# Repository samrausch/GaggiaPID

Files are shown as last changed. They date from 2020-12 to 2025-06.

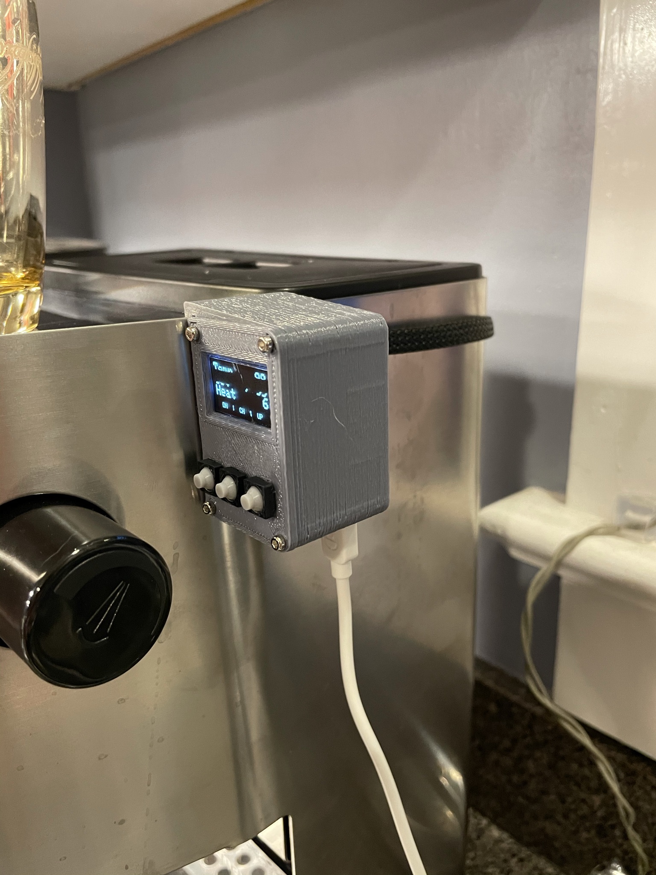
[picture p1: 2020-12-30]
Photos/IMG_0123.JPEG

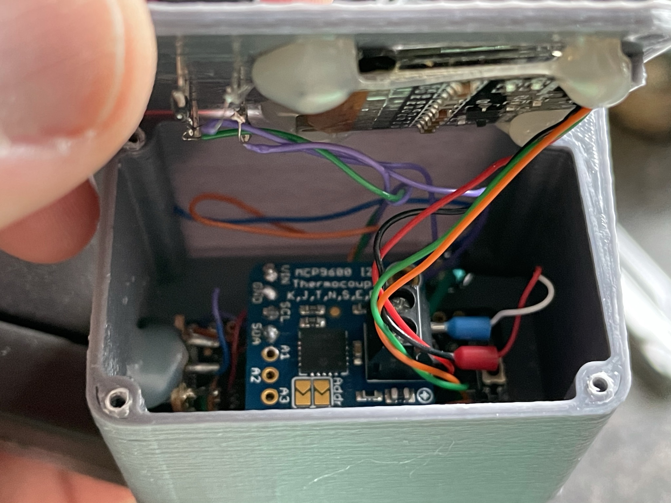
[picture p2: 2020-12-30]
Photos/IMG_0134.JPEG

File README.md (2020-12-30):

# GaggiaPID
Open Source PID for Gaggia Classic and Classic Pro espresso machines

As seen on https://www.reddit.com/r/gaggiaclassic/comments/kmm09a/diy_pid_for_my_gaggia_classic/

The .ino file includes several libraries.  Please make sure you've downloaded them prior to uploading the code to your Arduino of choice.  This was built on an Adafruit Metro Mini, which is directly compatible with the Arduino Uno R3, but you can use any Arduino board as long as it has enough pins and it supports I2C.

The code is reasonably well commented internally and variables are named such that it should be easy to find values you may need to change for your specific implementation, such as which pins have buttons assigned to them or the output pin for the SSR.

This design is intended to be as simple as possible in terms of the installation, and requires minimal modification to the Gaggia machine.  You'll need the following parts, as well as basic soldering tools/skills and access to a 3D printer (if you choose to use the included .stl files)

* Arduino board of your choice
* MCP9600 thermocouple amp (https://www.adafruit.com/product/4101)
* M4 threaded K-type thermocouple (widely available from Amazon, etc as a replacement part for 3D printers)
* 128x64 I2C OLED screen (substitute any screen you prefer but you'll need to update the code for your specific unit)
* 3 buttons (I used these: https://www.aliexpress.com/item/32811149954.html?spm=a2g0s.9042311.0.0.49554c4dRzoluB)
* M2x8mm screws of your choise (I used these: https://www.amazon.com/gp/product/B00YBMRAH4/ref=ppx_yo_dt_b_search_asin_title?ie=UTF8&psc=1)
* Solid state relay (I used this: https://www.amazon.com/gp/product/B07Y33RZ8F/ref=ppx_yo_dt_b_search_asin_title?ie=UTF8&psc=1)
* Rare earth magnets (optional), attached to the back of the SSR to fasten it to the inside of the espresso machine.
* Braided cable sleeve (optional), I used https://www.amazon.com/gp/product/B07QJW9FKS/ref=ppx_yo_dt_b_search_asin_title?ie=UTF8&psc=1

# 3D printing

I printed everything using Inland PLA+ filament.  Pretty much any material should work fine as the outside of the Gaggia never gets hot enough to melt most thermoplastics.  The included STL files assume you're using the exact same parts I am.  If you use anything different you'll need to make adjustments to the 3D printed parts.

There are no holes in the printed parts for the wiring between the PID and espresso machine, you'll need to decide where you want these holes and drill them yourself.

In it's current revision, the Arduino board is still powered via USB so there needs to be an opening to plug in the USB cable.  This opening is also not included in the STL files as it's easier to locate the hole during the assembly.

# Assembly

Follow the included circuit diagram.  For the wiring inside the PID I just used 32AWG single strand hookup wire and for any wiring inside the Gaggia I used silicone insulated wire (26AWG for the wiring from PID to SSR, 12AWG to extend the thermoswitch leads to the SSR as referenced in the Installation Steps below).  The boiler in the Gaggia can get hot enough to melt non-silicone insulation so if you don't have silicone wiring, make sure to keep any wiring well clear of the boiler.

The Arduino board is secured using a small amount of hot glue.  The MCP9600 board is fastened with a screw to the small ledge inside the 3D printed box.  The OLED and buttons can be secured with your favorite adhesive.  The lid of the enclosure is held by four screws.  I drilled pilot holes for all the screws because my 3D printer has problems printing holes that small.  You will probably want to drill pilot holes as well to prevent cracking the plastic.

My PID is just held on by the clip on the side of the 3D printed box.  Gravity seems to be working as expected in my case but you may decide to attach a magnet to the side of the box that touches the Gaggia for a more secure mount.  If you do this, consider counter-sinking the magnet so that it is flush with the outisde of the box.  This will keep things looking tidy.

# Installation steps:

* THIS ASSUMES YOUR COMPETENT WORKING WITH AC CIRCUITS.  AC CIRCUITS ARE DANGEROUS AND MISTAKES CAN CAUSE INJURY OR DEATH.  YOU ALONE ARE RESPONSIBLE FOR YOUR OWN SAFETY, PLEASE KNOW YOUR LIMITS.
* Remove the top of the machine and locate the boiler thermal switch.  This will be the one at the bottom of the boiler, closest to the group head.
* Remove this thermal switch and replace it with the M4 thermocouple, making sure to add thermal compound if necessary.  The thermocouple should be snug but not too tight as the threads are not super robust.
* Run the TC leads out through the back of the machine and into the PID, attaching to the MCP9600.
* Connect the two leads you removed from the original thermal switch to the switched AC side of the SSR.  You may need to extend the leads depending on where you decide to mount the SSR.  They are not polarized so you can connect either one to either terminal of the SSR.
* Connect the +/- leads from the PID to the SSR input terminals, paying attention to the polarity as these are DC.
* Mount the SSR as desired.
* Optionally, you can add some sleeving to the wires running between the Gaggia and the PID.  If you do this, secure a zip tie to the end of the sleeve inside the machine to keep it from pulling out.
* Test that everything is working before closing the machine back up.

There's a circuit diagram included in the repo.  You're welcome to wire your PID however you like but make sure to change any pin numbers in the code to reflect how you've assembeled the circuit.

The PID has been setup with values for Kp, Ki and Kd that work adequately but you may want to adjust them to suit your needs.  The PID values are not saved if you change them through the menu so if you find a tuning you like and want to change the defaults, you'll need to do that in the code and then re-upload it to the device.

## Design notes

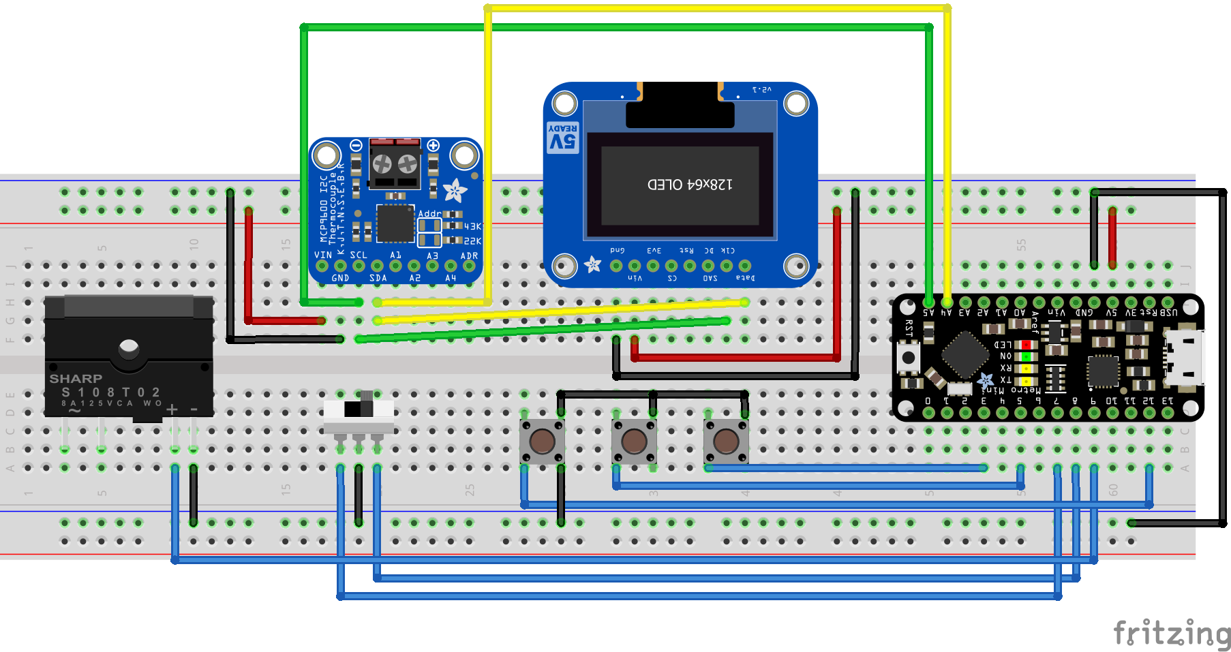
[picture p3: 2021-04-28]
GaggiaPID_circuit.png

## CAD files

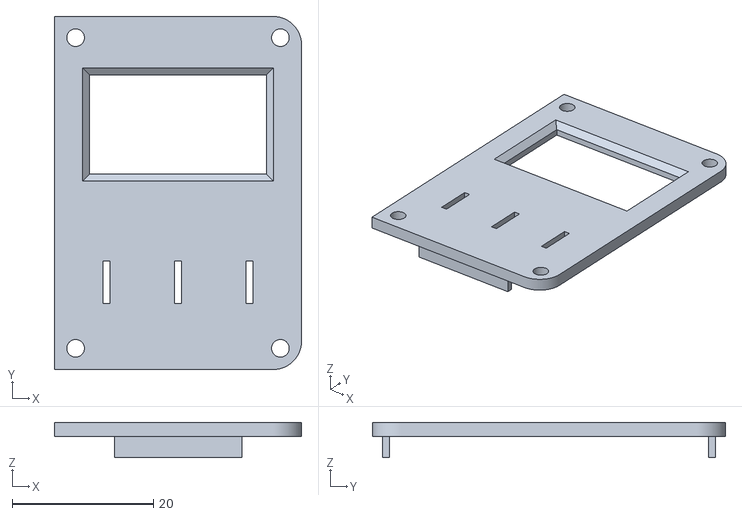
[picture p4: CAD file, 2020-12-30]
GaggiaPID_top.stl
35.0 x 50.0 x 5.00

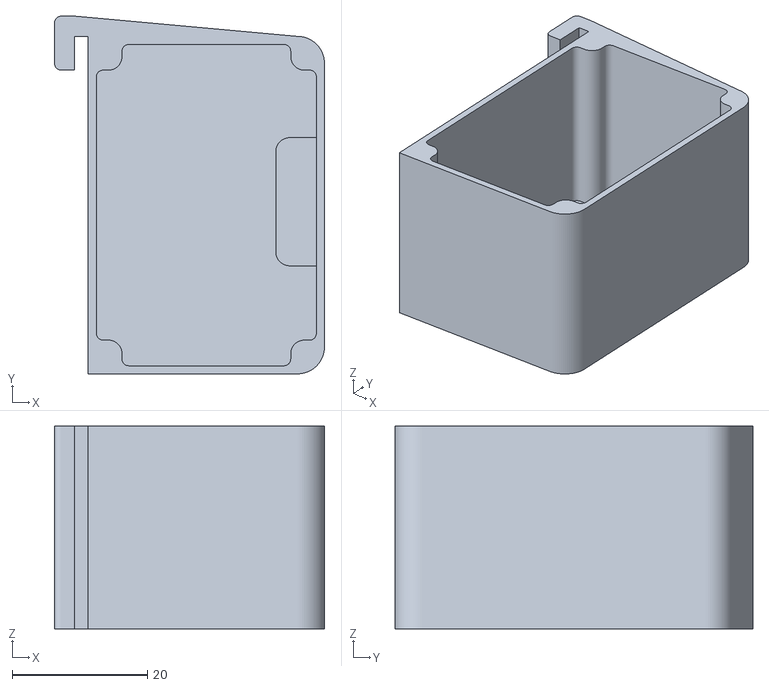
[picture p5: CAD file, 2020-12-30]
GaggiaPID_body.stl
40.0 x 53.0 x 30.0

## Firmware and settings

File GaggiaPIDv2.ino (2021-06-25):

#include <Adafruit_MCP9600.h>
#define tc_address (0x67)
Adafruit_MCP9600 mcp;

#include <Bounce2.h>
Bounce modeButton = Bounce();
Bounce upButton = Bounce();
Bounce downButton = Bounce();
const unsigned long intervalMs = 5;

#define NOOP __asm__ __volatile__ ("nop\n\t")

// if you're using a 128x64 i2c OLED, this is all you need
// if you're using something else, feel free to substitute your stuff here
#include <Adafruit_SSD1306.h>
#include <gfxfont.h>
#include <Adafruit_GFX.h>
#define SCREEN_WIDTH 128 // OLED display width, in pixels
#define SCREEN_HEIGHT 64 // OLED display height, in pixels
#define OLED_RESET 4
Adafruit_SSD1306 display(SCREEN_WIDTH, SCREEN_HEIGHT, &Wire, OLED_RESET);

#include <Wire.h> 
// This stuff is just for text formatting so you can control the indents and line spacing
// if you're using a 128x64 OLED screen, you can keep all these values
// otherwise you'll want to change them depending on your display
const int indent1 = 88;
const int indent2 = 72;
const int bottom = 56;
const int line1 = 0;
const int line2 = 16;
const int line3 = 32;
const int upPin = 3;
const int modePin = 12;
const int downPin = 5;
const int relayPin = 9;
const int runPin = 7;
const int progPin = 8;
int brewTemp = 93;      // set the default brew temp here
int steamTemp = 155;    // set the default steam temp here
int runMode = 1;
int brewMode = 1;
int firstRun = 1;

#include <PID_v1.h>
double targetTemp;
double currentTemp;
double heatState;
double Kp = 10;
double Ki = 50;
double Kd = 30;
PID myPID(&currentTemp, &heatState, &targetTemp, Kp, Ki, Kd, DIRECT);
int WindowSize = 100;
unsigned long windowStartTime;

void setup() {
  pinMode(relayPin, OUTPUT);
  pinMode(runPin, INPUT_PULLUP);
  pinMode(progPin, INPUT_PULLUP);
  display.begin(SSD1306_SWITCHCAPVCC, 0x3C);
  display.clearDisplay();
  display.setCursor(0,0);
  display.setTextSize(2);
  display.setTextColor(WHITE);
  display.println("Gaggia PID");
  display.println("v2.0");
  display.println("Now with STEAM!");
  if (! mcp.begin(tc_address)) {
    display.clearDisplay();
    display.println("TC ERROR");
    display.display();
    while (1);
  }
  mcp.setADCresolution(MCP9600_ADCRESOLUTION_18);
  mcp.setThermocoupleType(MCP9600_TYPE_K);
  mcp.setFilterCoefficient(3);
  mcp.enable(true);
  
  display.display();
  
  delay(1000);
  display.clearDisplay();
  display.setCursor(0,0);
  display.setTextSize(2);
  display.println("Temp");
  display.println("Set -->");
  display.println("Heat");
  display.setCursor(0,bottom);
  display.setTextSize(1);
  display.print("  DN  |  ST  |  UP  ");
  display.display();
  pinMode(modePin, INPUT_PULLUP);
  pinMode(upPin, INPUT_PULLUP);
  pinMode(downPin, INPUT_PULLUP);
  modeButton.attach(modePin);
  modeButton.interval(intervalMs);
  upButton.attach(upPin);
  upButton.interval(intervalMs);
  downButton.attach(downPin);
  downButton.interval(intervalMs);
  windowStartTime = millis();
  targetTemp = brewTemp;
  myPID.SetOutputLimits(0, WindowSize);
  myPID.SetMode(AUTOMATIC);
}

void brewDisplay() {
  // this function updates the display when in brew/steam mode
  display.clearDisplay();
  display.setCursor(0,0);
  display.setTextSize(2);
  display.println("Temp");
  if (brewMode == 1) {
    display.println("Brew  >");
  }
  if (brewMode == 2) {
    display.println("Steam >");
  }
  display.println("Heat");
  display.setCursor(indent1,line1);
  if (currentTemp < 100){
    display.print(" ");
  }
  display.print(int(currentTemp));
  display.setCursor(indent1,line2);
  if (targetTemp < 100){
    display.print(" ");
  }
  display.print(int(targetTemp));
  display.setCursor((indent1-12),line3);
  int heatDuty = map(heatState, 0, WindowSize, 0, 100);
  if (heatDuty < 1000){
    display.print(" ");
  }
  if (heatDuty < 100){
    display.print(" ");
  }
  if (heatDuty < 10){
    display.print(" ");
  }
  display.print(int(heatDuty));
  display.setCursor(0,bottom);
  display.setTextSize(1);
  display.print("  DN  |  ST  |  UP  ");
  display.display();
}

void PIDdisplay() {
  // this function updates the display when it's in programming mode
  display.clearDisplay();
  display.setCursor(0,0);
  display.setTextSize(2);
  display.println("P ");
  display.println("I ");
  display.println("D ");
  display.setCursor(indent2,line1);
  display.print(int(Kp));
  display.setCursor(indent2,line2);
  display.print(int(Ki));
  display.setCursor(indent2,line3);
  display.print(int(Kd));
  display.setCursor(0,bottom);
  display.setTextSize(1);
  display.print("  DN  |  CH  |  UP  ");
  display.setTextSize(2);
  switch (runMode) {
    case 1:
      display.setCursor(0,line1);
      display.print("  -->");
      break;
    case 2:
      display.setCursor(0,line2);
      display.print("  -->");
      break;
    case 3:
      display.setCursor(0,line3);
      display.print("  -->");
  }
  display.display();
}

void checkButtons() {
  // there's a lot going on in here
  // first we check the buttons to see if they've been pressed
  int modeSelect = 1;
  byte modeButtonState = modeButton.read();
  byte upButtonState = upButton.read();
  byte downButtonState = downButton.read();
  int amIrunning = digitalRead(runPin);
  // this is the swtich that goes between run and programming, connected to the runPin
  if (amIrunning == 0) {
    modeSelect = 1; //brewing
    brewDisplay();
  } else {
    modeSelect = 2; //programming
    PIDdisplay();
  }
  switch (modeSelect) {
    case 1: // we're brewing
      modeButton.update();
      modeButtonState = modeButton.read();
      // this section changes between steam and brew based on the brewMode variable, which is toggled by the mode button
      if (modeButtonState == LOW && modeButton.fallingEdge()) {
        switch (brewMode) {
          case 1: // Switch to steam
            brewMode = 2;
            brewTemp = targetTemp;
            targetTemp = steamTemp;
            //brewDisplay();
            break;
          case 2: // Switch to brew
            brewMode = 1;
            steamTemp = targetTemp;
            targetTemp = brewTemp;
            //brewDisplay();
        }
      }
      upButton.update();
      upButtonState = upButton.read();
      // here we're raising the temp of brew or steam
      if (upButtonState == LOW && upButton.fallingEdge()) {
        switch(brewMode) {
          case 1: // Adjust brew temp settings
            targetTemp++;
            //brewDisplay();
            break;
          case 2: // Adjust steam temp settings
            targetTemp++;
            //brewDisplay();    
        }
      }
      downButton.update();
      downButtonState = downButton.read();
      // here we're lowering the temp of brew or steam
      if (downButtonState == LOW && downButton.fallingEdge()) {
        switch(brewMode) {
          case 1: // Adjust brew temp settings
            targetTemp--;
            //brewDisplay();
            break;
          case 2: // Adjust steam temp settings
            targetTemp--;
            //brewDisplay();
        }
      }
      break;
    case 2: // we're programming
      modeButton.update();
      modeButtonState = modeButton.read();
      // since we're in programming mode, the buttons now control the PID variables
      if (modeButtonState == LOW && modeButton.fallingEdge()) {
        switch (runMode) {
          case 1: // Switch to Ki setting
            runMode = 2;
            //PIDdisplay();
            break;
          case 2: // Switch to Kd setting
            runMode = 3;
            //PIDdisplay();
            break;
          case 3: // Switch to Kp setting
            runMode = 1;
            //PIDdisplay();
        }
      }
      upButton.update();
      upButtonState = upButton.read();
      if (upButtonState == LOW && upButton.fallingEdge()) {
        switch(runMode) {
          case 1: // Adjust Kp settings
            Kp++;
            myPID.SetTunings(Kp, Ki, Kd);
            //PIDdisplay();
            break;
          case 2: // Adjust Ki setting
            Ki++;
            myPID.SetTunings(Kp, Ki, Kd);
            //PIDdisplay();
            break;
          case 3: // Adjust Kd setting
            Kd++;
            myPID.SetTunings(Kp, Ki, Kd);
            //PIDdisplay();       
        }
      }
      downButton.update();
      downButtonState = downButton.read();
      if (downButtonState == LOW && downButton.fallingEdge()) {
        switch(runMode) {
          case 1: // Adjust Kp settings
            Kp--;
            myPID.SetTunings(Kp, Ki, Kd);
            //PIDdisplay();
            break;
          case 2: // Adjust Ki setting
            Ki--;
            myPID.SetTunings(Kp, Ki, Kd);
            //PIDdisplay();
            break;
          case 3: // Adjust Kd setting
            Kd--;
            myPID.SetTunings(Kp, Ki, Kd);
            //PIDdisplay();
        }      
      }
  }
}

void loop() {
  checkButtons();   // see in-line documentation in the function above
  if (millis() - windowStartTime > WindowSize)
    // this is where we periodically read the TC, update the PID and then reset the timer for the next cycle
  { 
    currentTemp = mcp.readThermocouple();
    analogWrite(relayPin, map(heatState, 0, 100, 0, 1023));
    myPID.Compute();
    windowStartTime += WindowSize;
    if (firstRun) {
      delay(1000);
      brewDisplay();
      firstRun = 0;
    }
  }
}

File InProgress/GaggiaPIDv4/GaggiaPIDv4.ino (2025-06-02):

//#define debug

#include <WiFi.h>
#include <WiFiClient.h>
#include <WebServer.h>
#include <LEAmDNS.h>

#ifndef STASSID
#define STASSID "wifi_network"
#define STAPSK "wifi_password"
#endif

const char* ssid = STASSID;
const char* password = STAPSK;

WebServer server(80);

#include <Adafruit_MCP9600.h>
#define tc_address (0x67)
Adafruit_MCP9600 tc;

#include <Bounce2.h>
Bounce2::Button modeButton = Bounce2::Button();
Bounce2::Button upButton = Bounce2::Button();
Bounce2::Button downButton = Bounce2::Button();
//Bounce modeButton = Bounce();
//Bounce upButton = Bounce();
//Bounce downButton = Bounce();
int modePushCounter = 0;
int modeDebounced = 0;
int modeLastDebounced = 0;
bool modePressed = false;
const unsigned long intervalMs = 5;

#define NOOP __asm__ __volatile__("nop\n\t")

#include <Adafruit_SSD1306.h>
#include <gfxfont.h>
#include <Adafruit_GFX.h>

#define SCREEN_WIDTH 128
#define SCREEN_HEIGHT 64
#define OLED_RESET 4
Adafruit_SSD1306 display(SCREEN_WIDTH, SCREEN_HEIGHT, &Wire, OLED_RESET);

#include <Wire.h>

const int indent1 = 88;
const int indent2 = 72;
const int bottom = 56;
const int line1 = 0;
const int line2 = 16;
const int line3 = 32;
const int upPin = 27;    // Pi Pico pin
const int modePin = 26;  // Pi Pico pin
const int downPin = 28;  // Pi Pico pin
const int relayPin = 9;  // Pi Pico pin
int operatingMode = 1;   // 1=brew 2=steam
int configureMode = 1;   // 1=operate 2=configure
int PIDparam = 1;        // 1=Kp 2=Ki 3=Kd
int steamTemp = 140;     // default steam temp
int brewTemp = 85;       // default brew temp


#include <PID_v1.h>
double targetTemp;
double currentTemp;
double heatState;
double Kp = 70;
double Ki = 0.1;
double Kd = 1;
PID myPID(&currentTemp, &heatState, &targetTemp, Kp, Ki, Kd, DIRECT);
int WindowSize = 500;
int calcSize = 250;
unsigned long windowStartTime;
unsigned long calcStartTime;


void setup() {
  Serial.begin(9600);
#ifdef debug
  Serial.println("Debugging enabled...");
#endif
  Wire.setSDA(0);
  Wire.setSCL(1);
  Wire.begin();
  pinMode(relayPin, OUTPUT);
  display.begin(SSD1306_SWITCHCAPVCC, 0x3C);
  display.clearDisplay();
  display.setCursor(0, 0);
  display.setTextSize(2);
  display.setTextColor(WHITE);
  display.println("Gaggia PID");
  display.println("Pico");
  display.println("v1.0");
  delay(2000);
  if (!tc.begin(tc_address)) {
    display.clearDisplay();
    display.println("TC_mcp ERROR");
    display.display();
    while (1)
      ;
  }
  tc.setADCresolution(MCP9600_ADCRESOLUTION_18);
  tc.setThermocoupleType(MCP9600_TYPE_K);
  tc.setFilterCoefficient(3);
  tc.enable(true);
  pinMode(modePin, INPUT_PULLUP);
  modeButton.attach(modePin);
  modeButton.interval(intervalMs);
  modeButton.setPressedState(LOW);
  pinMode(upPin, INPUT_PULLUP);
  upButton.attach(upPin);
  upButton.interval(intervalMs);
  upButton.setPressedState(LOW);
  pinMode(downPin, INPUT_PULLUP);
  downButton.attach(downPin);
  downButton.interval(intervalMs);
  downButton.setPressedState(LOW);
  windowStartTime = millis();
  calcStartTime = millis();
  targetTemp = brewTemp;
  myPID.SetOutputLimits(0, WindowSize);
  myPID.SetMode(AUTOMATIC);
  WiFi.mode(WIFI_STA);
  WiFi.begin(ssid, password);
  Serial.println("");

  // Wait for connection
//  while (WiFi.status() != WL_CONNECTED) {
//    delay(500);
//    Serial.print(".");
//  }
  Serial.println("");
  Serial.print("Connected to ");
  Serial.println(ssid);
  Serial.print("IP address: ");
  Serial.println(WiFi.localIP());

//  if (MDNS.begin("gaggiapid")) {
//    Serial.println("MDNS responder started");
//  }
  server.on("/", handleRoot);
  server.onNotFound(handleNotFound);
  server.on("/inline", []() {
    server.send(200, "text/plain", "this works as well");
  });
  server.begin();
  Serial.println("HTTP server started");
}

void loop() {
#ifdef debug
  Serial.print(configureMode);
  Serial.print(",");
  Serial.print(operatingMode);
  Serial.print(",");
  Serial.println(PIDparam);
#endif
  server.handleClient();
  MDNS.update();
  checkButtons();
  updateDisplay();
  runPID();
}

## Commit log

2020-12-30 Fritzing file
    [GaggiaPID.fzz]
2021-03-27 Fixed several items, added SPDT switch for programming
    Replaced OLED with correct part, fixed incorrect ground on buttons, added SPDT switch to support programming since the middle button is now for activating steam.
    [GaggiaPID.fzz]
2021-04-28 Cleanup and added features
    Added steam control, moved PID adjustments to a different menu accessed using the new SPST switch indicated in the new Fritzing diagram. Fixed a couple stupid things I did the first time
    [GaggiaPIDv2.ino]
